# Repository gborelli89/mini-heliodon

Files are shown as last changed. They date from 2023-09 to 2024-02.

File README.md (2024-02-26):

# mini-heliodon
Projeto de Heliodon de pequenas dimensões com controle automático para usos educacionais.

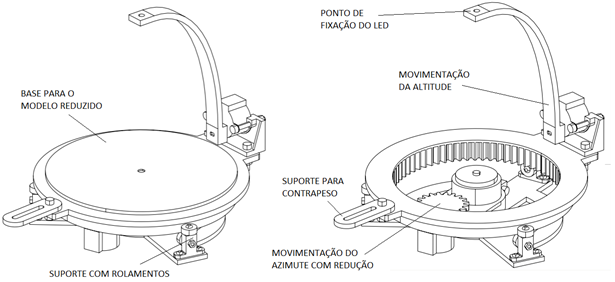
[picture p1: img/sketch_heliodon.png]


Os arquivos STL podem ser baixados e impressos em uma impressora 3D. Alguns elementos como lâmpada LED, acoplamentos, motores de passo e rolamentos devem ser comprados. O projeto deve ser usado como referência. Foi desenvolvido pensando em um dispositivo de pequenas dimensões, que facilite sua fabricação (em impressoras 3D de filamento caseiras, por exemplo) e manuseio. Deve ser adaptado para cada necessidade. 

Na tabela abaixo é dada a lista de materiais básicos necessários para a construção do heliodon na escala proposta.

| DESCRIÇÃO | QUANT. |
| --- | -----: |
| Motor de passo 28BYJ-48 | 2 |
| Driver de motor de passo ULN2003 | 2 |
| LED branco de alto brilho 5 mm | 1 |
| Resistor 100 &Omega; | 1 |
| Chave liga/desliga (opcional) | 1 |
| Fonte chaveada 5 V 1 A e conector | 1 |
| Arduino Uno (ou outro microcontrolador) | 1 |
| Rolamento 623ZZ | 6 |
| Parafuso M4 x 12 mm | 2 |
| Parafuso M4 x 20 mm | 5 |
| Parafuso M4 x 30 mm | 2 |
| Porca M4 | 9 |
| Arruela M4 | 13 |
| Parafuso M3 x 10 mm | 9 |
| Parafuso M3 x 16 mm | 3 |
| Porca M3 | 12 |
| Chapa de madeira (ou outro material) revestida de branco &empty;150 mm x 3 mm | 1 |
| Filamento de PLA (ou outro material, dependendo da impressora) | &asymp; 150 g |
| | |

## Controle
Para este projeto foram empregados dois motores de passo, um para movimentação do azimute e outro para a movimentação da altura. O controle é feito por meio de um microcontrolador (código na pasta *src*). O esquema básico de ligação é mostrado na figura abaixo.

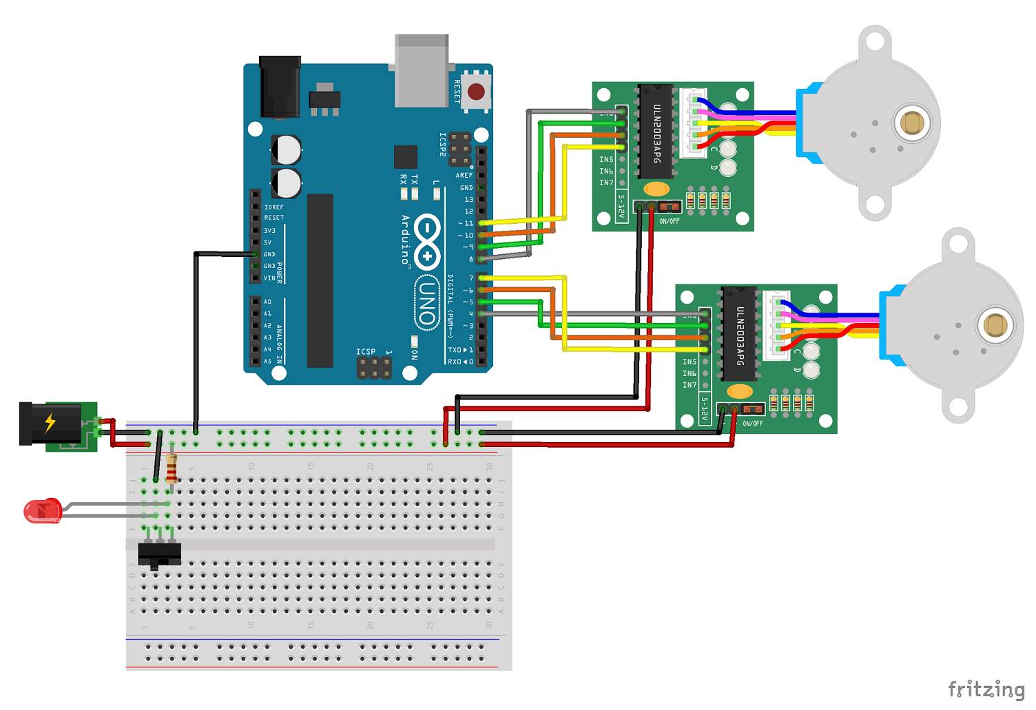
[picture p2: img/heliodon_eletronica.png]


## *Software*

### Pacotes necessários

É necessário possuir python instalado. As bibliotecas necessáriarias são apresentadas abaixo com a última versão testada entre parênteses. Recomenda-se que sua instalação seja feita em ambiente virtual, utilizando o PIP:

```
pip install package_name
```

* numpy (1.26.4)
* pandas (2.2.1)
* pysolar (0.11)
* plotly (5.19.0)
* pyserial (3.5)
* dash (2.15.0)
* waitress (3.0.0)

### Simulações implementadas

* ***onepoint_sim***: simulação de uma posição solar, dada latitude, longitude, data e horário.
* ***oneday_sim***: simulação da posição solar em um dia completo, hora a hora, dada latiture, longitude e data.
* ***month_sim***: simulação da posição solar mês a Mês, para a mesma posição geográfica (latitude e longitude), ano, dia e hora.

As simulações podem ser executadas diretamente a partir da linha de comando. Para isso basta importar o arquivo *heliodon.py*, fazer a conexão, determinar a altitude e o azimute com uma das simulações e utilizar a função *move* para mover o heliodon. Um exemplo de movimentação única e simples é dado abaixo.

```
import heliodon as sun

con = sun.connect('COM1') # modificar de acordo com a porta

# Simulação simples de uma posição
x = sun.onepoint_sim(-23.5, -46.7, 2023, 3, 20, 12, utcdiff=-3)

# Movimentação do heliodon
sun.move(con, float(x.latitude.iloc[0]), float(x.altitude.iloc[0]), float(x.azimuth.iloc[0]))
```

Caso deseje verificar as portas conectadas (com o objetivo de identificar a porta em que o microcontrolador está conectado), utilize a função *serial_ports()*, disponível em *heliodon.py*.

Para facilitar o uso, foi criada uma interface gráfica, que pode ser utilizada carregando diretamente o arquivo *heliodon_app.py*, ou seja, 

```
C:\> python heliodon_app.py
```

A interface gráfica gera diagramas como o apresentado na figura abaixo.

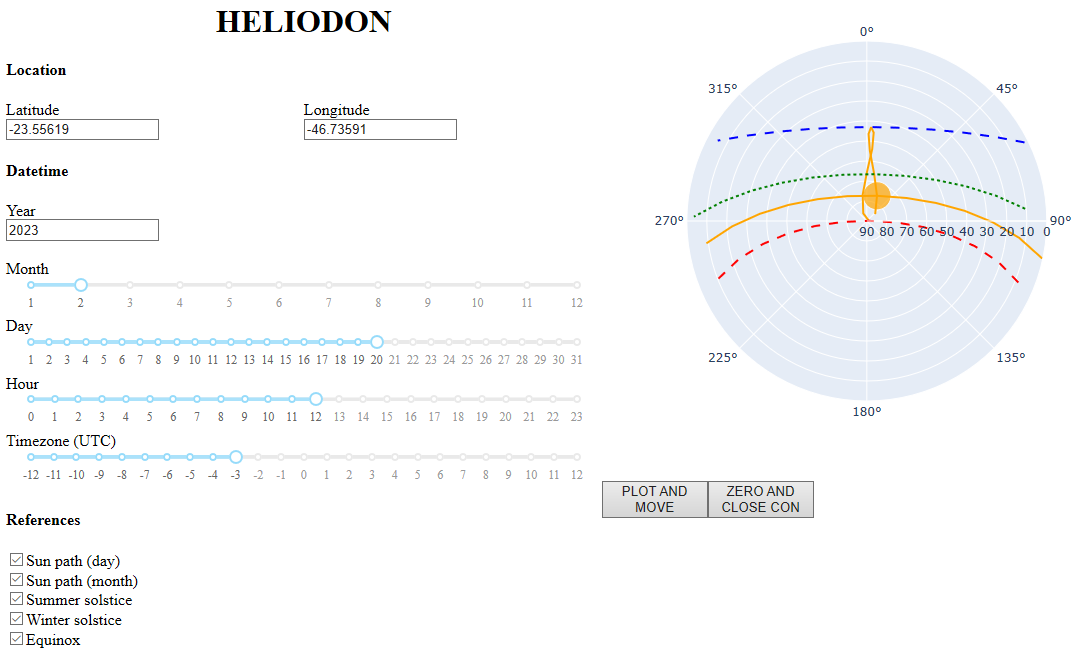
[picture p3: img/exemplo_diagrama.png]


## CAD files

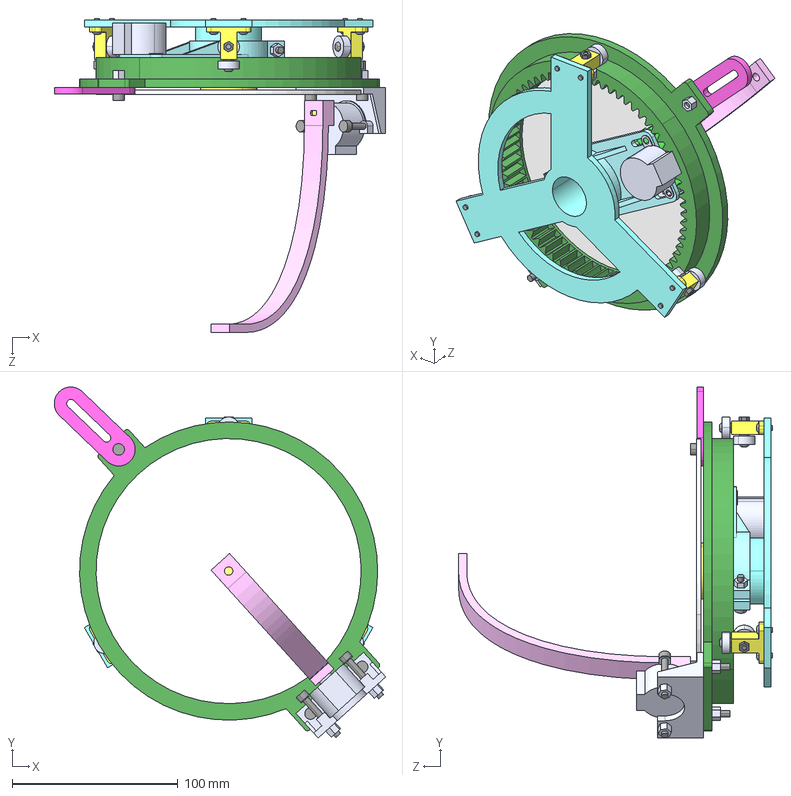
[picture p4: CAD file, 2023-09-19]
projeto_mecanico/Montagem.STEP
200.1 x 211.9 x 189.5 mm
base
suporte_eng_externa x 3
porcaM3 x 6
rolamento_4mm x 6
parafusoM3x8 x 9
arruelaM3 x 3
parafusoM3x16 x 3
suporte_motor_az
motorPasso x 2
pino_motor x 2
eng_interna_v3
eng_externa
suporte_motor_alt
arco
parafusoM4x20 x 3
porcaM4 x 6
parafusoM4x30 x 2
contrapeso
parafusoM4x12
espacador
mesa

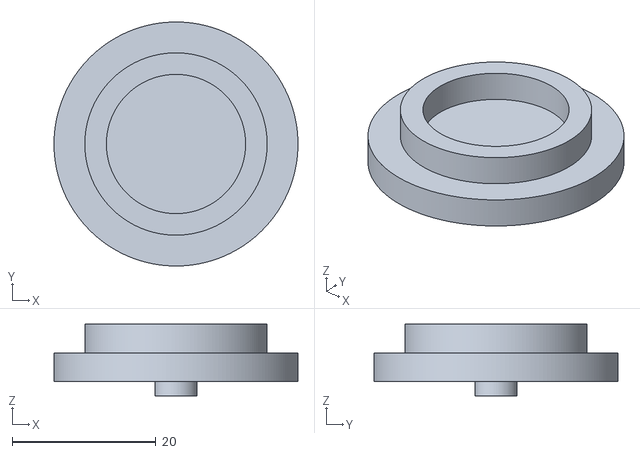
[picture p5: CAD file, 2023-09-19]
projeto_mecanico/stl/espacador.STL
34.0 x 34.0 x 10.0

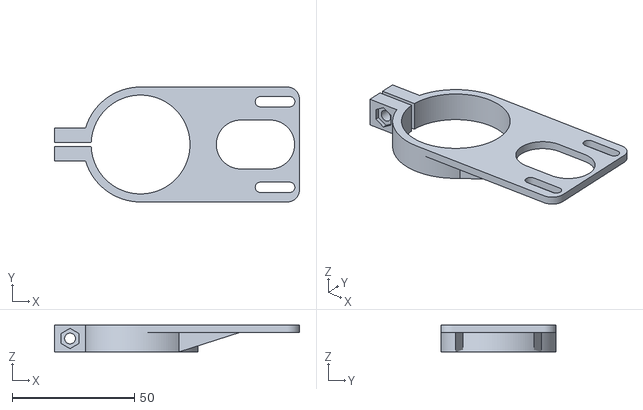
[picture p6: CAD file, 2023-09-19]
projeto_mecanico/stl/suporte_motor_az.STL
100.2 x 47.0 x 11.0

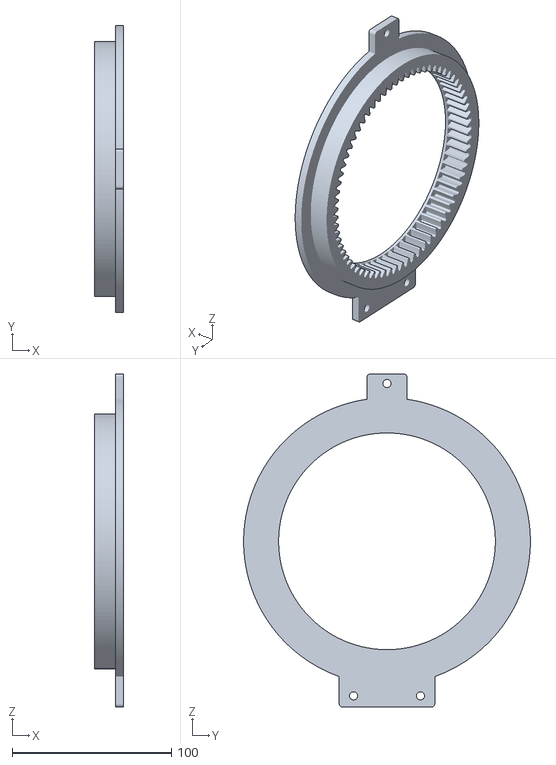
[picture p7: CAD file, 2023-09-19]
projeto_mecanico/stl/eng_externa.STL
18.0 x 180.0 x 209.0

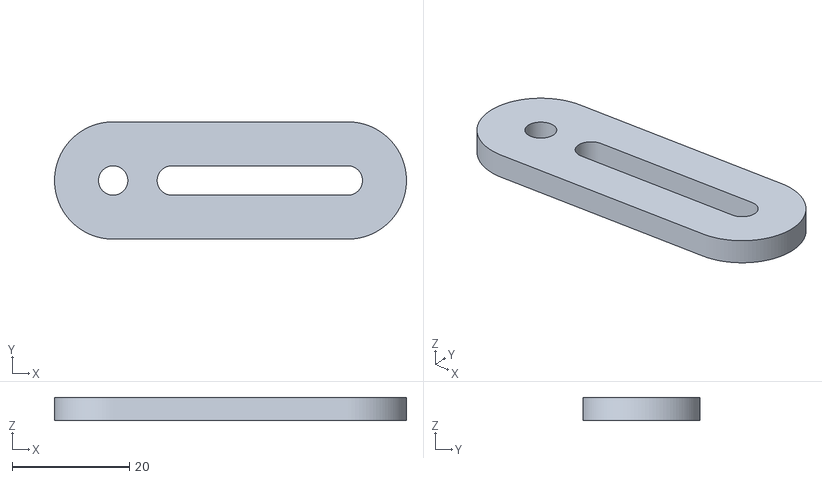
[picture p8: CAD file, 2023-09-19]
projeto_mecanico/stl/contrapeso.STL
60.0 x 20.0 x 4.00

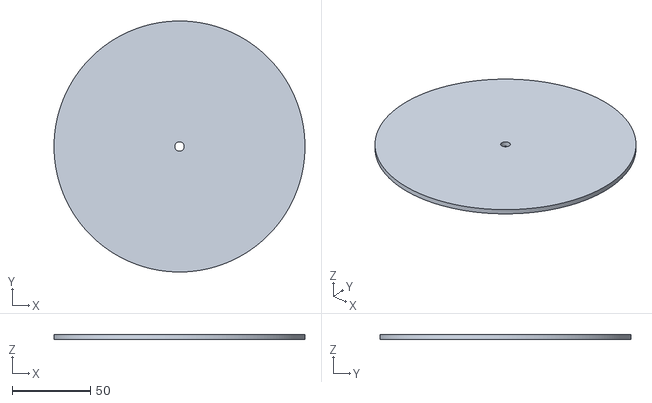
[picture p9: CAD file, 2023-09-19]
projeto_mecanico/stl/mesa.STL
160.0 x 160.0 x 3.00

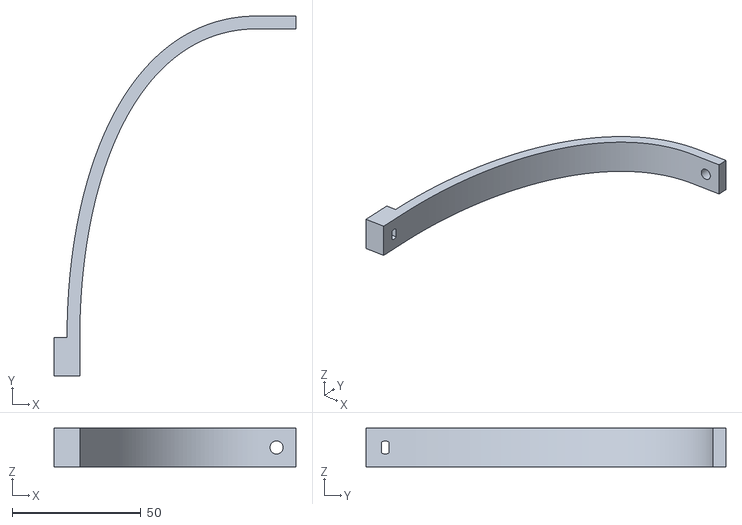
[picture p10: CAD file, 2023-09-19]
projeto_mecanico/stl/arco.STL
94.0 x 140.0 x 15.0

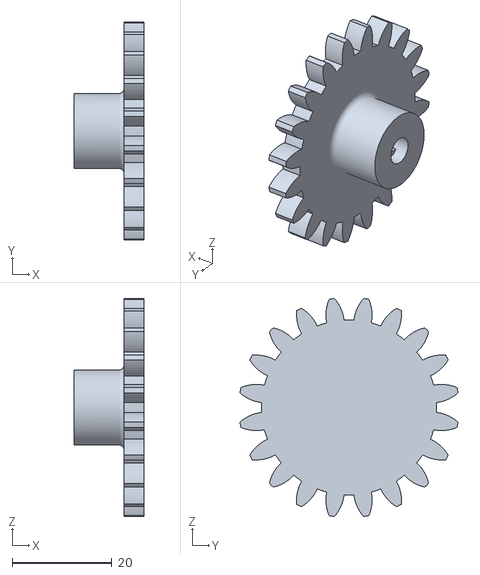
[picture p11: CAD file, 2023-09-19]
projeto_mecanico/stl/eng_interna_v3.STL
14.0 x 43.6 x 43.6

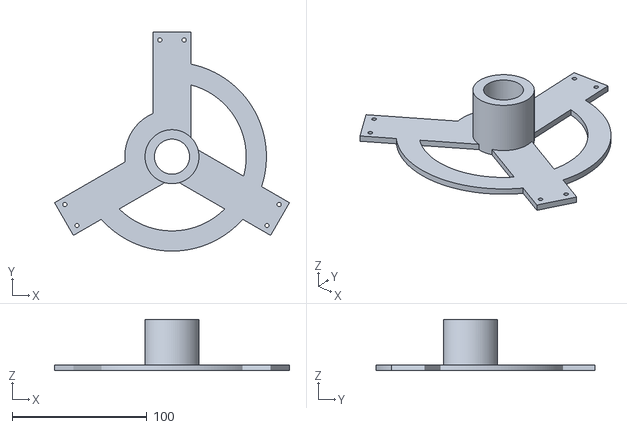
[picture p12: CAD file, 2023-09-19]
projeto_mecanico/stl/base.STL
174.2 x 162.5 x 38.0

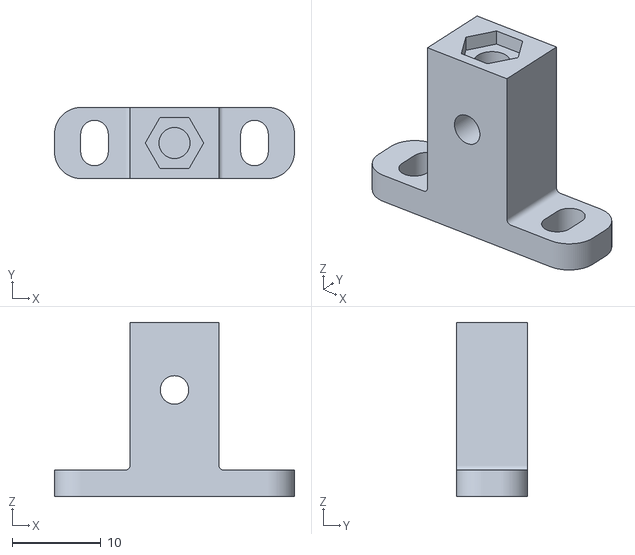
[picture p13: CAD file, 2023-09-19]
projeto_mecanico/stl/suporte_eng_externa.STL
27.0 x 8.00 x 19.6

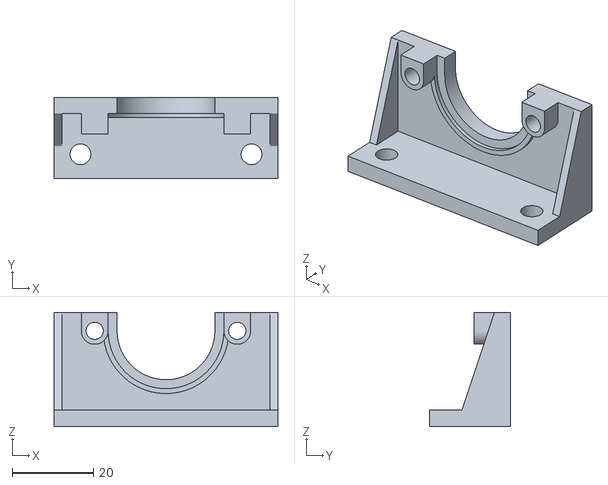
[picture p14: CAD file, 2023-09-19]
projeto_mecanico/stl/suporte_motor_alt.STL
55.0 x 20.0 x 28.0

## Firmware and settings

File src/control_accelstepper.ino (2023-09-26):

#include <AccelStepper.h>
#include <MultiStepper.h>

#define HALFSTEP 8

// Define some steppers and the pins the will use
AccelStepper stepperAltitude(HALFSTEP, 4,5,6,7);
AccelStepper stepperAzimuth(HALFSTEP, 8,9,10,11);

MultiStepper steppers;

void setup()
{  
    Serial.begin(9600);
    
    stepperAltitude.setMaxSpeed(300.0);
    stepperAzimuth.setMaxSpeed(300.0);

    steppers.addStepper(stepperAltitude);
    steppers.addStepper(stepperAzimuth);

    //Serial.print("Ready");
    //Serial.print("\n\n");

}

void loop()
{
    String msg_status = "NA";
    String v1 = "NA";
    String v2 = "NA";
    String dt = "NA"; 
    int stepper_status = 0;
    
    long positions[2];

    Serial.write(stepper_status);

    if(Serial.available()){

        String msg_status = Serial.readStringUntil(';');
        String v1 = Serial.readStringUntil(';');
        String v2 = Serial.readStringUntil(';');
        String dt = Serial.readStringUntil('\n');
        
        int valueAlt = v1.toInt();
        int valueAz = v2.toInt();
        int timeinterval = dt.toInt();

        if(msg_status=="movesun"){
          positions[0] = valueAlt;
          positions[1] = valueAz;
          //Serial.print("Moving system...");
          //Serial.print("\n");
          //Serial.print("Altitude value: ");
          //Serial.print(v1);
          //Serial.print("\n");
          //Serial.print("Azimuth value: ");
          //Serial.print(v2);
          //Serial.print("\n\n");
  
          stepper_status = 1;
          Serial.write(stepper_status);
          delay(100);
          
          
          steppers.moveTo(positions);
          steppers.runSpeedToPosition();
        
          if(stepperAzimuth.distanceToGo() < 5){
            delay(timeinterval);
            //stepper_status = 0;
            //Serial.write(stepper_status);
            //Serial.print("Ready");
            //Serial.print("\n\n");
            //delay(500);
          }
    
        }
    }

     delay(100);

}

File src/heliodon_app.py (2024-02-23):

import os
import sys
import dash
from dash import dcc, html
from dash.dependencies import Input, Output, State
import heliodon as sun
import webbrowser
from threading import Timer
from waitress import serve

# App

app = dash.Dash(__name__)

server = app.server

def open_browser():
    """
    Open browser to localhost
    """

    webbrowser.open_new('http://127.0.0.1:8080/')


# Layout

app.layout = html.Div([

    html.Div(children=[
        
        html.H1(
            children='HELIODON',
            style={
                'textAlign': 'center'
            }
        ),
        
        html.H4('Location'),
        html.Div([
            html.Label("Latitude"),
            html.Br(),
            dcc.Input(id='LAT', value='latitude', type='text')
        ], style={'width':'50%', 'display':'inline-block'}),
        html.Div([
            html.Label("Longitude"),
            html.Br(),
            dcc.Input(id='LON', value='longitude', type='text'),            
        ], style={'width':'50%', 'float':'right'}),

        html.H4('Datetime'),
        html.Label('Year'),
        html.Br(),
        dcc.Input(id='y', value='year', type='text'),
        html.Br(),
        html.Br(),
        html.Label('Month'),
        html.Br(),
        dcc.Slider(1,12,1, value=6, id='m'),
        html.Label('Day'),
        html.Br(),
        dcc.Slider(1,31,1, value=15, id='d'),

        html.Label('Hour'),
        html.Br(),
        dcc.Slider(0,23,1, value=10, id='h'),
        html.Label('Timezone (UTC)'),
        html.Br(),
        dcc.Slider(-12,12,1, value=0, id='utc'),

        html.H4('References'),
        dcc.Checklist(
            options={
                'sp_day': 'Sun path (day)',
                'sp_month': 'Sun path (month)',
                'sol_summer': 'Summer solstice',
                'sol_winter': 'Winter solstice',
                'equinox': 'Equinox'
            },
            value=['sp_day'],
            id='refpath'
        ),

    ], style={'width':'45%', 'display':'inline-block'}),

    html.Div([

        dcc.Graph(
            id = 'sunmap',
            style={'height':500}
        ),
        html.Div([
           html.Button('PLOT AND MOVE', id='move_show', n_clicks=0), 
        ], style={'width':'20%', 'float':'left'}),
        html.Div([
            html.Button('ZERO AND CLOSE CON', id='zero', n_clicks=0),
        ], style={'width':'20%', 'float':'left'})     

    ],style={'width':'40%', 'float':'right'})
    
], style={'display': 'flex', 'flex-direction': 'row'})


# Callback

@app.callback(
    Output('sunmap', 'figure'),
    Input('zero', 'n_clicks'), Input('move_show', 'n_clicks'),
    State('LAT', 'value'), State('LON','value'), State('y','value'), State('m','value'), 
    State('d','value'), State('h','value'), State('utc','value'), State('refpath', 'value')
)
def update_output_div(zero_clicks, moveshow_clicks, 
        lat_s, lon_s, y_s, m_s, d_s, h_s, tz_s, ref_s):

    if zero_clicks == 0 and moveshow_clicks == 0 :
        df = sun.nulldf(0,90)
        fig = sun.sun_position(df)
        return fig

    changed_id = [p['prop_id'] for p in dash.callback_context.triggered][0]

    if 'zero' in changed_id:
        if not(con.isOpen()):
            con.open()
        df = sun.nulldf(0,90)
        fig = sun.sun_position(df)
        sun.move(con, 0.0, df.altitude.iloc[0], df.azimuth.iloc[0], timeinterval=0)
        con.close()

    if 'move_show' in changed_id:
        if not(con.isOpen()):
            con.open()
        df = sun.onepoint_sim(float(lat_s), float(lon_s), int(y_s), int(m_s), int(d_s), int(h_s), int(tz_s))
        if df.altitude.iloc[0] >= 0:
            fig = sun.sun_position(df) 
            sun.add_path(fig, float(lat_s), float(lon_s), int(y_s), int(m_s), int(d_s), int(h_s), int(tz_s), pathtype=ref_s)
            sun.move(con, float(lat_s), df.altitude.iloc[0], df.azimuth.iloc[0], timeinterval=0)

    return fig
            

if __name__ == '__main__':

    available_ports = sun.serial_ports()
    port_id = range(len(available_ports))
    print("Port list: ")
    for n, v in zip(port_id, available_ports):
        print("{} -> {}".format(n, v))
    print("Port ID: ")
    id = int(input())
    con = sun.connect(available_ports[id])

    Timer(1, open_browser).start()
    serve(server)
    #app.run_server(debug=False)

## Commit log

2023-09-19 Arquivos STL e montagem
    Inseri arquivos STL das peças principais com montagem no formato STEP
    [Montagem.STEP, arco.STL, base.STL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]
2023-09-26 Algoritmos app e controlador
    Inseri alguns arquivos, como os algoritmos utilizados, código do app criado (dash) e código para o microcontrolador
    [Montagem.STEP, arco.STL, base.STL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]
